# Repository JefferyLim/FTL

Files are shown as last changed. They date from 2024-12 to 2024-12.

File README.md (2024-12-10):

# Follow the Light

Follow the Light (FTL) is the final project for ENG EC545. The goal of this project was to explore the different course topics. Our team decided to explore the ideas of a IR-based communication project. Taking inspiration from TeraByte InfraRed Delivery ([TBIRD](https://www.ll.mit.edu/sites/default/files/other/doc/2023-02/TVO_Technology_Highlight_12_TBird.pdf)), we wanted to create a system that would transmit data to a receiver. The receiver, would utilize the sensor data to track and follow the transmitter.

We implemented many concepts that we learned from the course such as:
1. Finite State Machines
  - In order to build the message transmitter (preamble -> payload -> crc), reciever's motor control, receiver's scanning mode, and receiver's message parser
2. Modeling
  - To validate our designs to make sure our logic makes sense and works
3. Timing Analysis and WCET
  - Ensure that our design (and microcontroller) is capable of meeting the timing needs for the system. The ADC is critical for every subcomponent in the receiver, so it must always sample on time 
4. Datasheet and Specs
  - Because we worked with new hardware, we needed to understand the specs to would help us with our specifications

## Installation

Install the [Arduino IDE](https://support.arduino.cc/hc/en-us/articles/360019833020-Download-and-install-Arduino-IDE) and the [Teensyduino](https://www.pjrc.com/teensy/td_download.html) add-on.

FTL utilizes the following libraries. Utilize the `Import ZIP Library` feature on the Arduino IDE.

[RingBuffer Library](https://github.com/Locoduino/RingBuffer)

[ADC Library](https://github.com/pedvide/ADC)

[CRC](https://github.com/RobTillaart/CRC)

## Architecture

### Transmitter
transmitter_system drawio
The transmitter can be set in one of three modes:
1. LED Mode - A simple 50% duty cycle square wave used mostly for testing.
2. Message Mode - Takes a user's input, and transmit the message out.
3. Counter Mode - Increments a counter, and transmits the number. 

The transmitter works similarly to UART. It has a start bit, 8 bit preamble, 8 bit payload, and 8 bit CRC. The payload could be longer, but we chose to use 8 bits in order to debug it. 

### Receiver

reciever_system drawio

The receiver is comprised of three subsystems:
1. ADC Sampling - Samples the 3 photodiodes at 5x the transmit rate
2. Message Parsing - Parses 5 samples at a time to determine a `1` or a `0` bit
3. Motor Control - Moves the motor to maintain sight to the transmitter

We oversample the recieving signal in order to conduct a vote on the value of a bit. A specific part of the hardware is unable to meet high throughput, causing major skewing in the signal when the signal goes from 0 to 1. 

### Project Structure

```
.
├── ...
├── documentation           # Documentation
│   ├── drawio              # drawio diagrams
├── modeling                # modeling
├── software                # software
│   ├── adc_test            # initial testing for ADCs
│   ├── irled_tests         # initial testing for the IR LEDs
│   ├── receiver            # receiver code
│   └── transmitter         # transmitter code
└── README.md
```

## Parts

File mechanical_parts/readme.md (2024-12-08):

# Summary
Mechanical design, all parts were created using SolidWorks 2020.

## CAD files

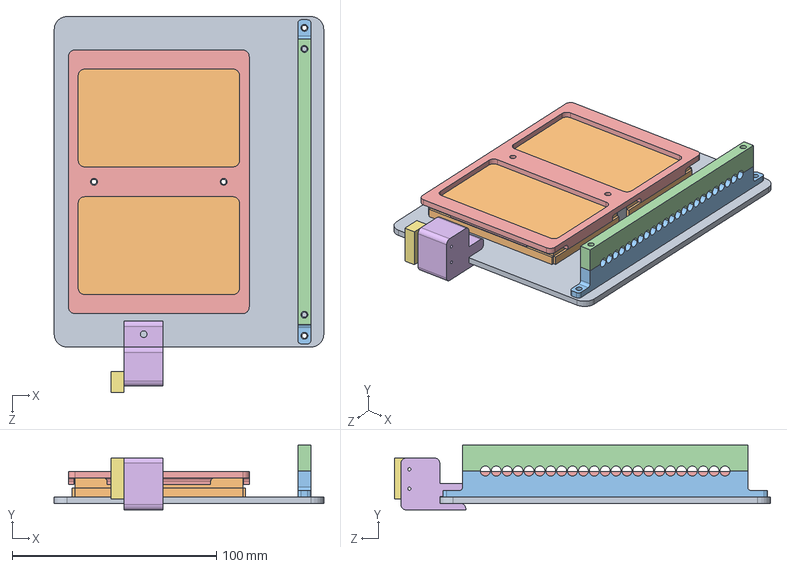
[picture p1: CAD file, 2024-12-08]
mechanical_parts/electronics assem.SLDASM
132.1 x 31.8 x 184.2 mm
electronics sled
small breadboard x 2
bottom_led_stockade
top_led_stockade
bb grabber
microswitch_holder
microswitch

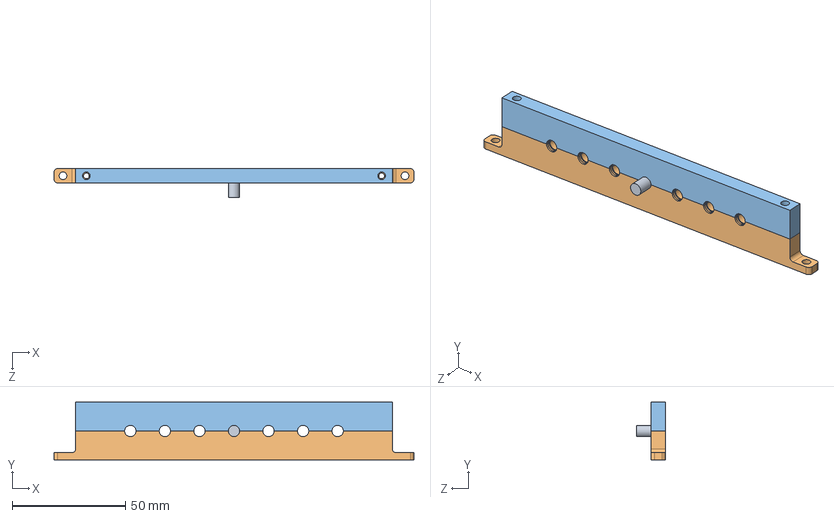
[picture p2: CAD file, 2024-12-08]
mechanical_parts/led_assem.SLDASM
158.8 x 25.4 x 12.7 mm
bottom_led_stockade v2
top_led_stockade v2

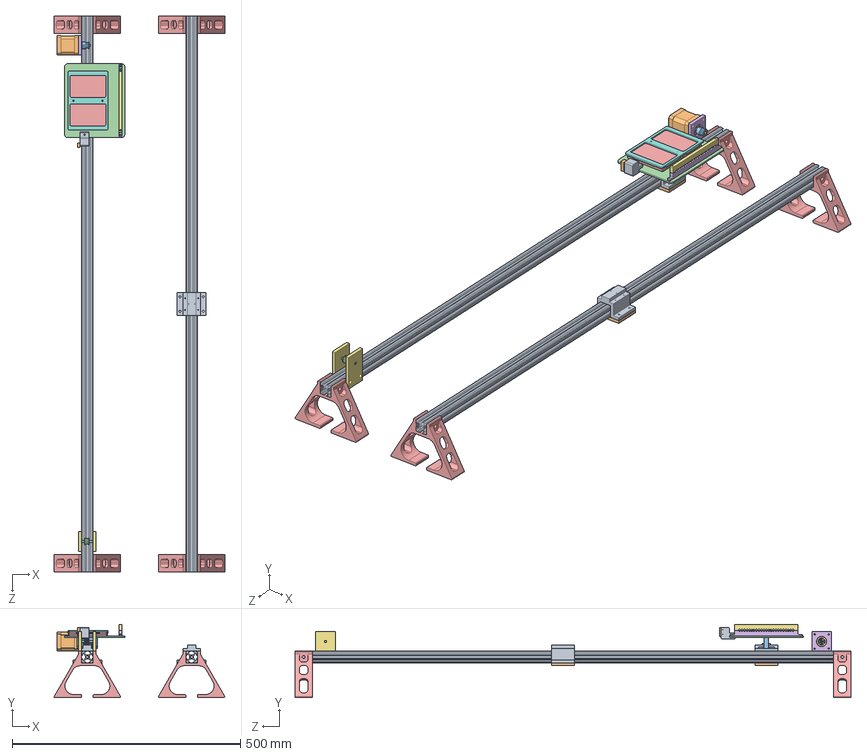
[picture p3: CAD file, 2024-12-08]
mechanical_parts/project_assem.SLDASM
374.6 x 160.1 x 1219.2 mm
47065T121_T-Slotted Framing x 2
nema_17_stepper
3684N12_Corrosion-Resistant HTD Timing Belt Pulley
3693N11_High-Strength HTD Timing Belt Idler Pulley
rail_support x 4
stepper plate
idler_plate x 2
idler_shaft
runner x 2
runner_bottom_plate x 2
runner_belt_grabber
electronics sled
small breadboard x 2
bottom_led_stockade
top_led_stockade
bb grabber
microswitch_holder
microswitch
attacher

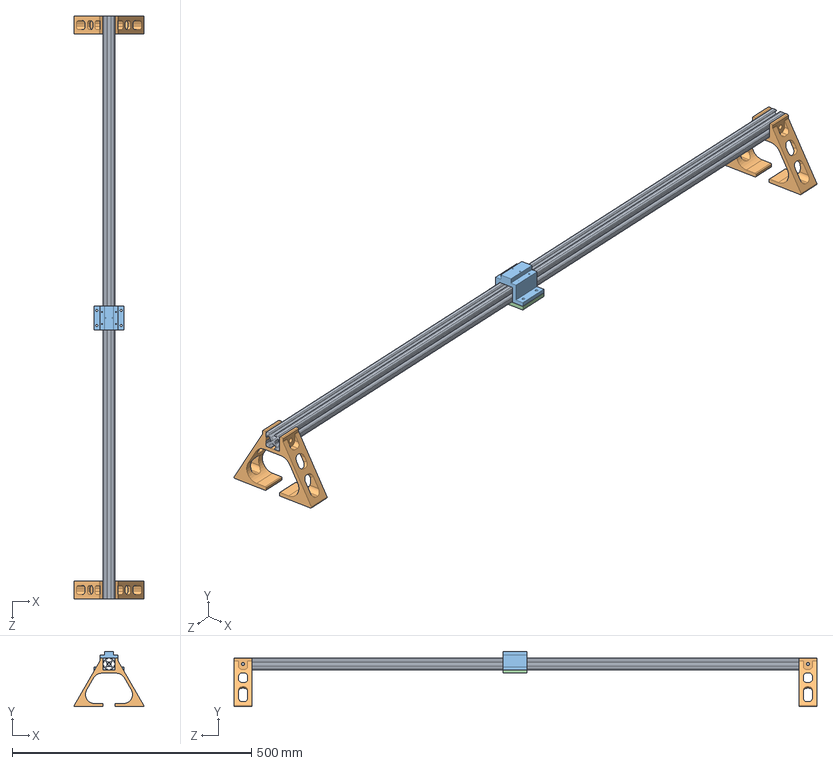
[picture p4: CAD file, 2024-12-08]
mechanical_parts/xmitter_assem.SLDASM
146.0 x 115.3 x 1219.2 mm
47065T121_T-Slotted Framing
rail_support x 2
runner
runner_bottom_plate

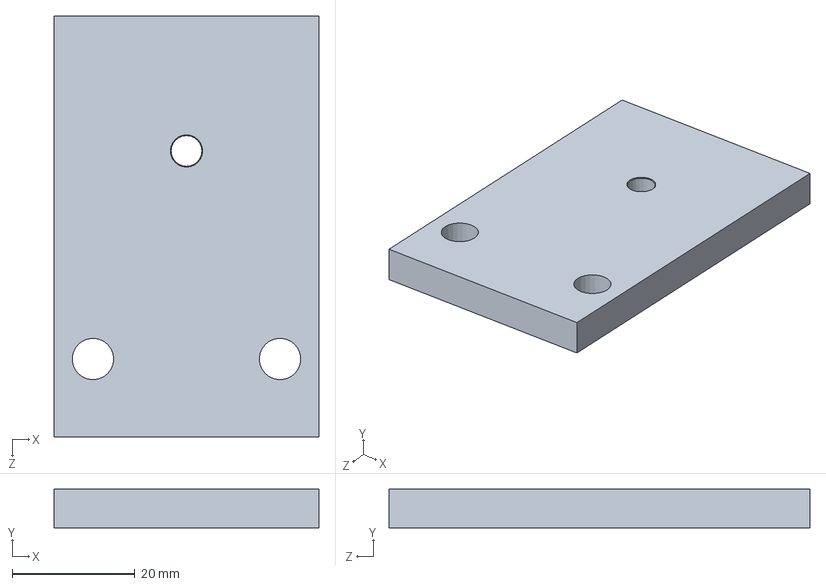
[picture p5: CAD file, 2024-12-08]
mechanical_parts/idler_plate.SLDPRT
43.2 x 6.35 x 68.6 mm

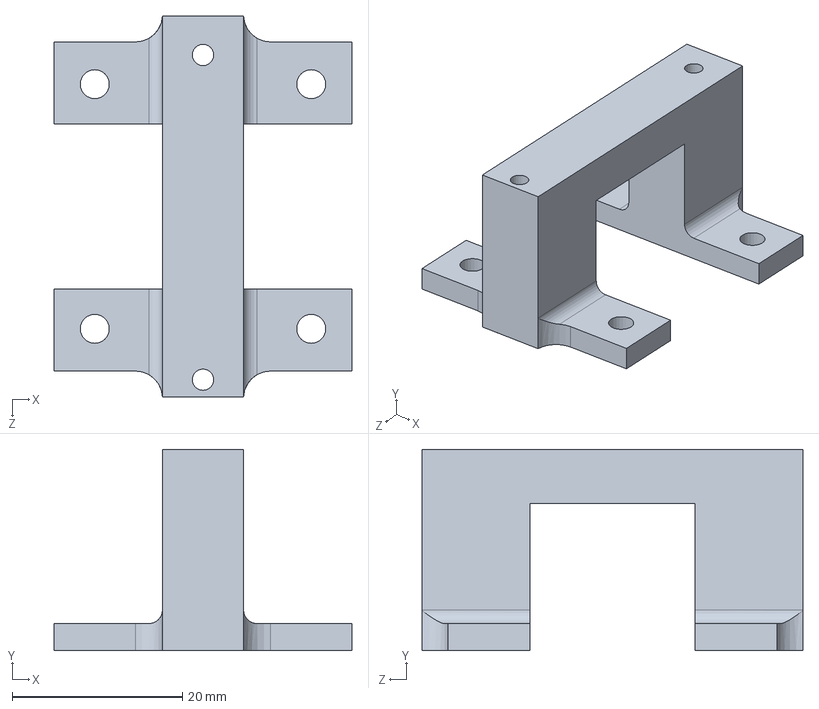
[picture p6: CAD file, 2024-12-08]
mechanical_parts/attacher.SLDPRT
34.9 x 23.6 x 44.7 mm

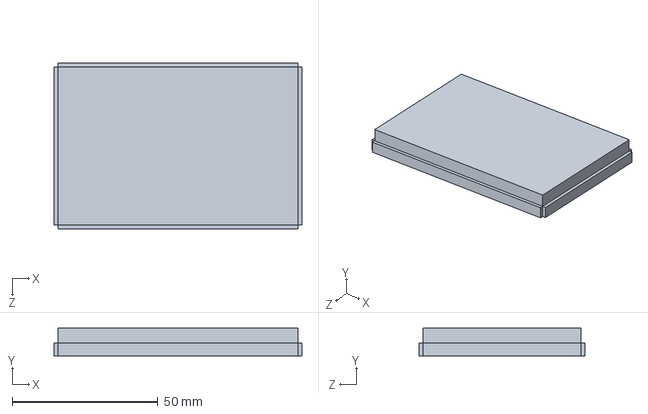
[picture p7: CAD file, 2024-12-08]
mechanical_parts/small breadboard.SLDPRT
84.9 x 9.53 x 57.0 mm

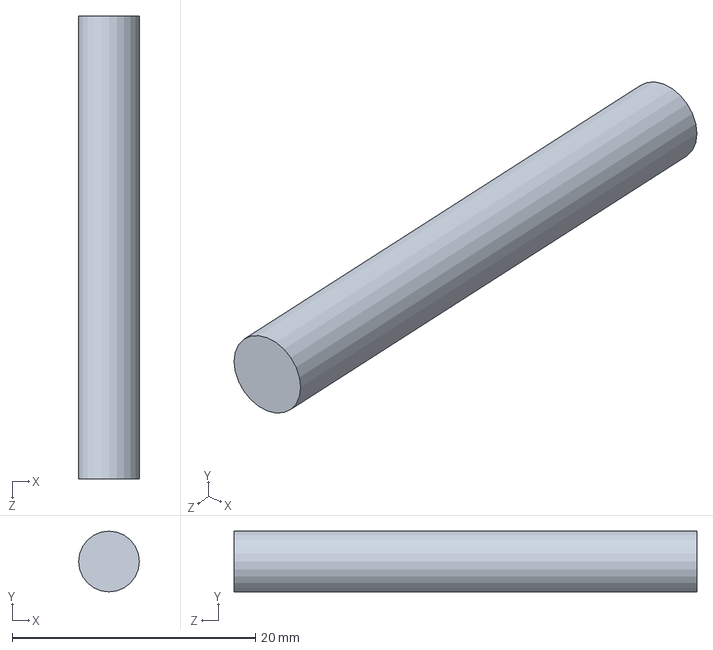
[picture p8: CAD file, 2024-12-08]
mechanical_parts/idler_shaft.SLDPRT
5.00 x 5.00 x 38.1 mm

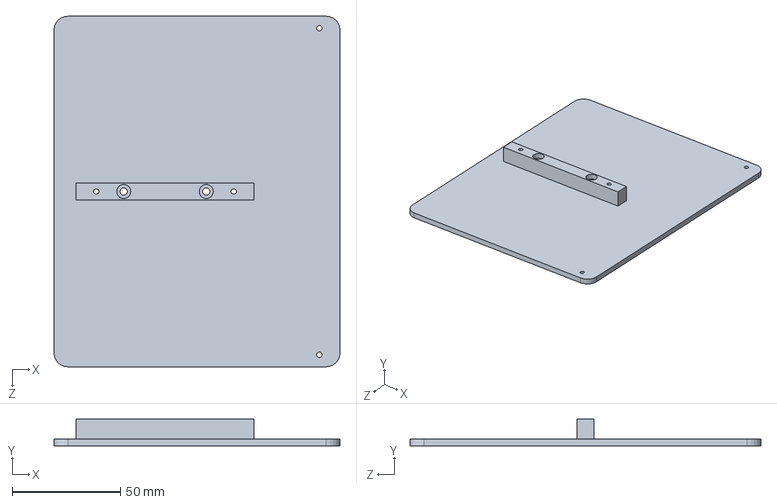
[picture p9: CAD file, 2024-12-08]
mechanical_parts/electronics sled.SLDPRT
132.1 x 12.4 x 161.9 mm

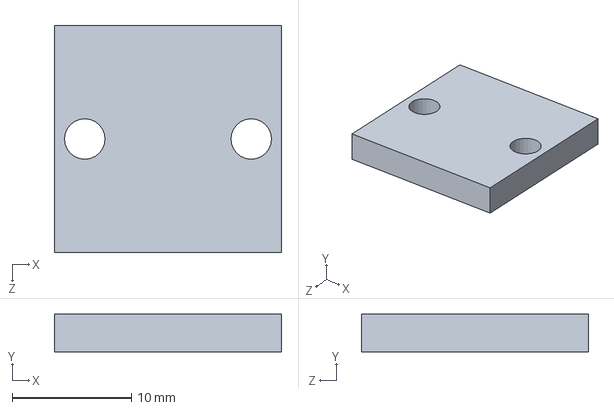
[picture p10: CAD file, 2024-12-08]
mechanical_parts/runner_belt_grabber.SLDPRT
19.1 x 3.17 x 19.1 mm

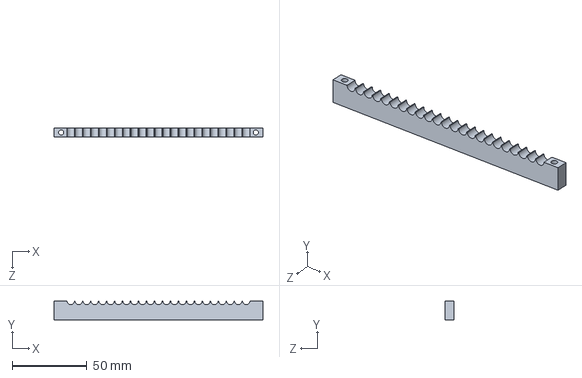
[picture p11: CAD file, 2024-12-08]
mechanical_parts/top_led_stockade.SLDPRT
139.7 x 12.7 x 6.35 mm

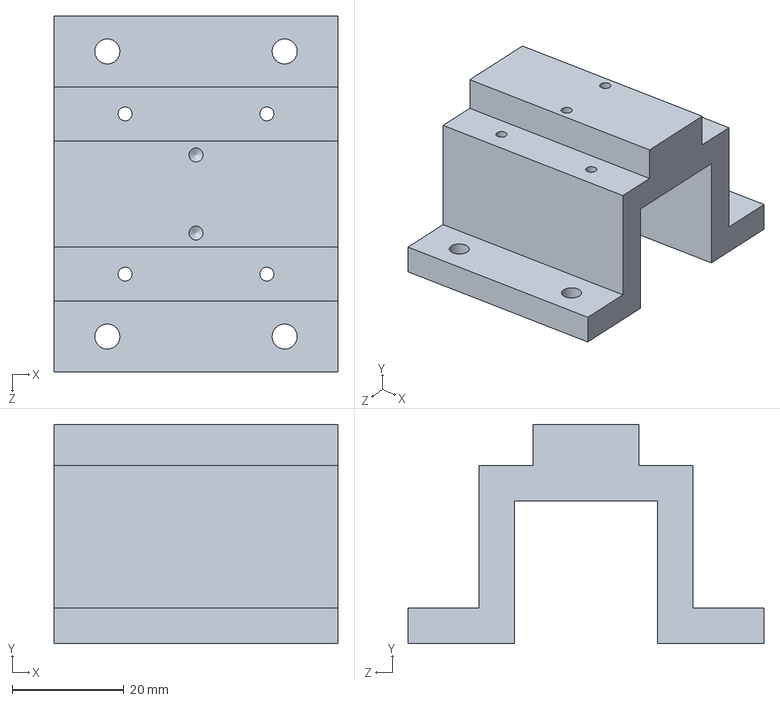
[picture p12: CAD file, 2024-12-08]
mechanical_parts/runner.SLDPRT
50.8 x 39.2 x 63.8 mm

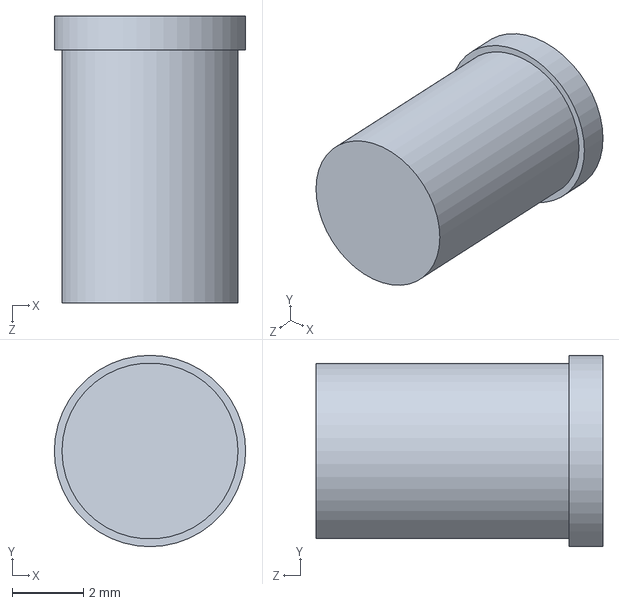
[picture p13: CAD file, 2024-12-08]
mechanical_parts/5mm_led_mock.SLDPRT
5.38 x 5.38 x 8.08 mm

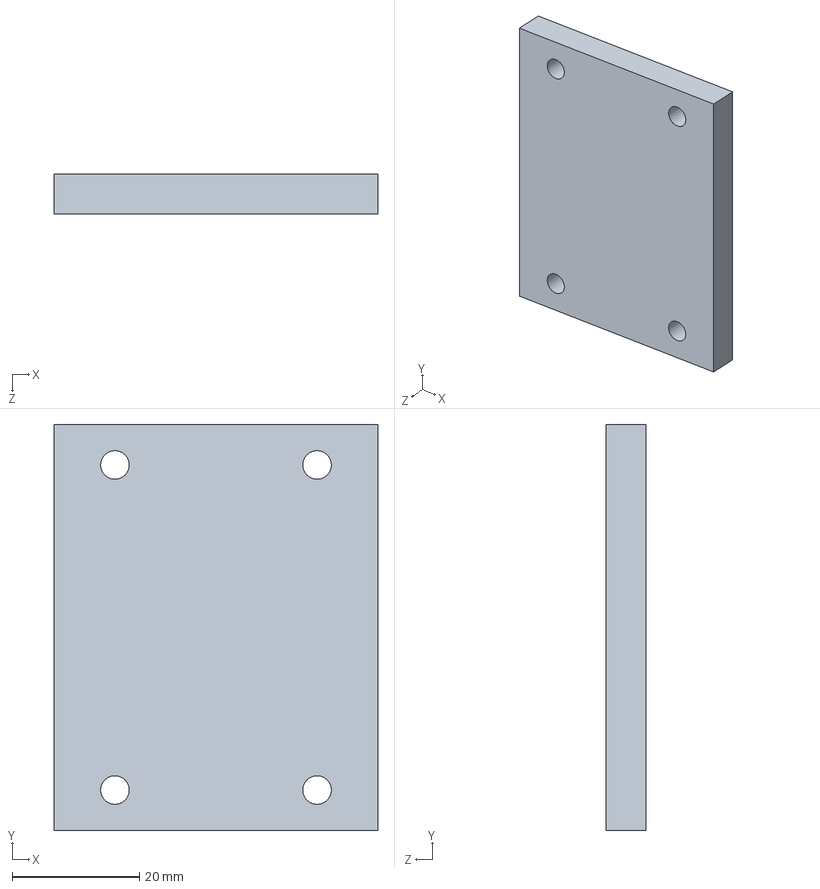
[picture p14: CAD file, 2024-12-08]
mechanical_parts/runner_bottom_plate.SLDPRT
50.8 x 63.8 x 6.35 mm

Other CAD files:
mechanical_parts/rail_support.SLDPRT
mechanical_parts/top_led_stockade v2.SLDPRT
mechanical_parts/microswitch_holder.SLDPRT
mechanical_parts/bottom_led_stockade.SLDPRT
mechanical_parts/3684N12_Corrosion-Resistant HTD Timing Belt Pulley.SLDPRT
mechanical_parts/3693N11_High-Strength HTD Timing Belt Idler Pulley.SLDPRT
mechanical_parts/47065T121_T-Slotted Framing.SLDPRT
mechanical_parts/6627T231_Stepper Motor.SLDPRT
mechanical_parts/bb grabber.SLDPRT
mechanical_parts/bottom_led_stockade v2.SLDPRT
mechanical_parts/microswitch.SLDPRT
mechanical_parts/nema_17_stepper.SLDPRT
mechanical_parts/stepper plate.SLDPRT

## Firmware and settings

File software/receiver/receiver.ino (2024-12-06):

#include "CRC8.h"

#define _PWM_LOGLEVEL_        0

#include <ADC.h>
#include <RingBuf.h>
#include <IntervalTimer.h>
#include <Teensy_PWM.h>

//Microswitch Pins
#define MOTOR_SIDE_SWITCH 22
#define OTHER_SIDE_SWITCH 21

#define USING_FLEX_TIMERS      true //Using flex timers for HW PWM

#define M2  9
#define M1  10
#define M0  11
#define STEP_PIN       7 //PWM Pins
#define DIR_PIN        6

//Threshold values
#define SENSOR_DIF_THRESH 200
#define SENSOR_SMALL_THRESH 50
#define SENSOR_BIG_THRESH 200

#define SENSOR_ON_THRESH 3600 // Sensor detecting for data
#define SENSOR_OFF_THRESH 3800 // Sensor not detecting for data

#define SENSOR_ABS_THRESH 3600 // Sensor not detecting for motor control

#define SAMPLING_FREQ 40000 // Hz
// Convert Sampling Frequency (Hz) to period (us)
double sampling_period = 1000000/SAMPLING_FREQ; // us

#define SAMPLING_RATIO 5 // SAMPLING_FREQ/
#define ON_THRESH 0 // SAMPLING_RATIO - ON_THRESH for 1's
#define OFF_THRESH 1  // OFF_THRESH for 0's

#define MOVEMENT_FREQ 500
 
//PRINT_SAMPLE, PRINT_RAW, PRINT_BIT, PRINT_CHAR, PRINT_SCAN, PRINT_NONE
#define PRINT_CHAR

//Timers (to emulate multithreading)
IntervalTimer sensor_readTimer;
IntervalTimer motor_controlTimer;

const int left_pin = A0;
const int mid_pin = A1;
const int right_pin = A2;

ADC *adc = new ADC(); 

//PWM Values:
float frequency;
float dutyCycle;

Teensy_PWM* stepper; //Stepper object


const int ledPin = LED_BUILTIN; // the pin with a LED

//States
enum tracking_state{
  SCANNING,
  LOCKED,
};

enum position_state{
  LEFT, MID_LEFT, MID, MID_RIGHT, RIGHT, UNKNOWN,
};

enum receiver_state{
  INIT,
  SYNCH,
  LOST,
};

enum message_state{
  START,
  MESSAGE,
  CRC,
  END,
};

//Sensor variables
//State variables
tracking_state track_state = SCANNING;
position_state pos_state;
message_state msg_state = START;
receiver_state rcv_state = INIT;

volatile char incoming_counter[10];
volatile int incoming_counter_counter = 0;
volatile int lost_counts = 0;
volatile int last_counter = -1;
volatile int current_counter = 0;

// Created photodiode array struct
struct photodiode_array{
  uint16_t left;
  uint16_t mid;
  uint16_t right;
  uint8_t bit : 1;
  uint8_t bit_confidence : 1;
  uint8_t : 3;
  uint8_t position : 3;
  
};

// RingBuffers
RingBuf<photodiode_array, 1024> adcBuffer; // for raw ADC outputs + other metrics
RingBuf<photodiode_array, 1024> bitBuffer; // extra buffer before message parsing
RingBuf<photodiode_array, 1024> motorBuffer; // extra buffer before motor control
RingBuf<int, 1024> messageBuffer; // buffer for collecting bits for message parsing

// Counters
int lostLockCount = 0;
int messageByteCount = 0;
int missingStartCounter = 0;

// Received Message
int receivedByte = 0;
int crcByte = 0;
CRC8 crc;
volatile int crc_index;
volatile int crccode;

// Flags
volatile bool bufferOverflow = 0;

// Performance Calcs
volatile int start = 0;
volatile int end = 0;

volatile unsigned long startMillis;
volatile unsigned long currentMillis;

// Position/Motor
int movement_counter = 0;
volatile position_state previous_position = MID;
volatile position_state last_known_state = MID;
int current_speed = 0;
bool hit_wall = false;
int button_debounce = 0;

void setup() {
  pinMode(left_pin, INPUT);
  pinMode(mid_pin, INPUT);
  pinMode(right_pin, INPUT);
  pinMode(ledPin, OUTPUT);
  Serial.begin(115200);

  ///// ADC0 ////
  adc->adc0->setAveraging(4); // set number of averages
  adc->adc0->setResolution(16); // set bits of resolution
  adc->adc0->setConversionSpeed(ADC_CONVERSION_SPEED::HIGH_SPEED); // change the conversion speed
  adc->adc0->setSamplingSpeed(ADC_SAMPLING_SPEED::HIGH_SPEED); // change the sampling speed

  ///// ADC1 ////
  adc->adc1->setAveraging(4); // set number of averages
  adc->adc1->setResolution(16); // set bits of resolution
  adc->adc1->setConversionSpeed(ADC_CONVERSION_SPEED::HIGH_SPEED); // change the conversion speed
  adc->adc1->setSamplingSpeed(ADC_SAMPLING_SPEED::HIGH_SPEED); // change the sampling speed

  sensor_readTimer.priority(0); //Set sensor priority higher
  motor_controlTimer.priority(1);
  
  sensor_readTimer.begin(read_sensors,(int)sampling_period); 
  motor_controlTimer.begin(pwm_control,(int)sampling_period*MOVEMENT_FREQ);

  //// PWM ////
  pinMode(DIR_PIN, OUTPUT);
  pinMode(M0, OUTPUT);
  pinMode(M1, OUTPUT);
  pinMode(M2, OUTPUT);
  stepper = new Teensy_PWM(STEP_PIN, 500, 0);
  /////

  //Microswitch pins
  pinMode(MOTOR_SIDE_SWITCH, INPUT_PULLUP);
  pinMode(OTHER_SIDE_SWITCH, INPUT_PULLUP);

}

void read_sensors() { //Read analog sensor input
  start = micros();
  struct photodiode_array dataset = {0}; 

  // difference variables
  // int edge_dif;
  // int left_mid_dif;
  // int mid_right_dif;

  dataset.left = adc->adc0->analogRead(left_pin);
  dataset.mid = adc->adc1->analogRead(mid_pin);
  dataset.right = adc->adc0->analogRead(right_pin);

  if(dataset.left <= SENSOR_ON_THRESH || dataset.right <= SENSOR_ON_THRESH \
   || dataset.mid <= SENSOR_ON_THRESH){
    dataset.bit = true;
    
    #ifdef PRINT_RAW
    Serial.print(1);
    #endif
    dataset.bit_confidence = true;
  }else if(dataset.left >= SENSOR_OFF_THRESH && dataset.right >= SENSOR_OFF_THRESH \
    && dataset.mid >= SENSOR_OFF_THRESH) {
    dataset.bit = false;
    dataset.bit_confidence = true;
    
    #ifdef PRINT_RAW
    Serial.print(0);
    #endif
  }else{
    
    #ifdef PRINT_RAW
    Serial.print(0);
    #endif
    dataset.bit = false;
    dataset.bit_confidence = false;
  }

  // edge_dif = dataset.left - dataset.right;
  // left_mid_dif = dataset.left - dataset.mid;
  // mid_right_dif = dataset.mid - dataset.right;

if(dataset.left > SENSOR_ABS_THRESH && dataset.mid > SENSOR_ABS_THRESH && dataset.right > SENSOR_OFF_THRESH){
    dataset.position = UNKNOWN;
  }else{

    if(dataset.mid < dataset.left && dataset.mid < dataset.right){
      dataset.position = MID; 
    }

    if(dataset.left < dataset.mid && dataset.left < dataset.right){
      dataset.position = LEFT; 
      if(abs(dataset.mid - dataset.left) < SENSOR_SMALL_THRESH){
        dataset.position = MID_LEFT;
      }
    }

    if(dataset.right < dataset.mid && dataset.right < dataset.left){
      dataset.position = RIGHT;
      if(abs(dataset.mid - dataset.right) < SENSOR_SMALL_THRESH){
        dataset.position = MID_RIGHT;
      }
    }
  }

  if(!adcBuffer.push(dataset)){
    Serial.println("ERROR: Can't push to buffer");
  }

  end = micros();
  // Serial.print("ADC: ");
  // Serial.println(end - start);
}

// Print function for printing the photodiode struct
void print_photodiode_struct(struct photodiode_array input){
  Serial.print(input.left);
  Serial.print(" | ");
  Serial.print(input.mid);
  Serial.print(" | ");
  Serial.print(input.right );
  Serial.print(" | ");
  Serial.print(input.bit );
  Serial.print(" | ");
  Serial.print(input.bit_confidence );
  Serial.print(" | ");
  printPosition(input.position);
  Serial.print(" | ");
  printPosition(last_known_state);
  Serial.println();
}

void printPosition(int input){
  switch (input) {
    case LEFT:
      Serial.print("LEFT");
      break;
    case MID_LEFT:
      Serial.print("MID_LEFT");
      break;
    case MID:
      Serial.print("MID");
      break;
    case MID_RIGHT:
      Serial.print("MID_RIGHT");
      break;
    case RIGHT:
      Serial.print("RIGHT");
      break;
    default:
      Serial.print("UNKNOWN");
      break;
  }
}

int bitShift = 0;
void messageParse(){
  struct photodiode_array adcValues;
  int bitCount = 0;
  int receivedBit = 0;

  // Double check that buffer is >5
  if(bitBuffer.size() < SAMPLING_RATIO){
    return;
  }

  // If we are in a "LOST" state... try and find presence of a signal...
  // A presence of a signal is 5 '1's or IR LED ON 
  if(rcv_state == LOST || rcv_state == INIT){
    
    digitalWriteFast(ledPin, 1);
    for(int i = 0; i < SAMPLING_RATIO; i++){
      // Look at the next 5 values
      bitBuffer.peek(adcValues, i);
      // Note, that if the bit confidence is high, then we can use the these samples
      // We only want to use 5 confident bits for now...
      if(adcValues.bit_confidence == 1){
        bitCount += adcValues.bit;
      }else{
        bitCount = 0;
        break;
      }
    }
  
    // If we find at least 4 '1' samples, lets start parsing
    // Move from LOST -> SYNCH
    if(bitCount >= (SAMPLING_RATIO - ON_THRESH)){
      #ifdef PRINT_CHAR
      Serial.println("Sync");
      #endif
      rcv_state = SYNCH;
      bitCount = 0;
      
      incoming_counter_counter = 0;
    }else{
      bitBuffer.pop(adcValues);
    }
  }else if(rcv_state == SYNCH){
    digitalWriteFast(ledPin, 0);
    // Begin counting bits
    for(int i = 0; i < SAMPLING_RATIO; i++){
      bitBuffer.pop(adcValues);
      bitCount += adcValues.bit;
    }

    // Do a majority vote
    // Anything inbetween is ambiguous, and we will exit SYNCH
    if(bitCount >= SAMPLING_RATIO - ON_THRESH){
      messageBuffer.push(1);
    }else if(bitCount <= OFF_THRESH){
      messageBuffer.push(0);
    }else{
      #ifdef PRINT_CHAR
      Serial.println();
      Serial.print("Ambiguous bits: ");
      Serial.print(bitCount);
      Serial.println("; returning to LOST...");
      #endif
      bitCount = 0;
      rcv_state = LOST;
      lostLockCount++;
      messageBuffer.clear();
      missingStartCounter = 0;
    }

    // Parse the bits for the message
    if (messageBuffer.size() > 6){
      if(msg_state == START) {
        missingStartCounter++;
        // If we dont' find the start within 1 second, then we exit SYNCH
        if(missingStartCounter > SAMPLING_FREQ/10){
          #ifdef PRINT_CHAR
          Serial.println("Can't find start bit...");
          Serial.println("Receiver can't find start bit; returning to LOST...");
          #endif
          messageBuffer.clear();
          missingStartCounter = 0;
          rcv_state = LOST;
        }else{
          bitCount = 0;
          // Look for a 111110
          for(int i = 0; i < 6; i++){
            messageBuffer.peek(receivedBit, i);
            if(i != 5 && receivedBit == 0){
              break;
            }
            if(i == 5 && receivedBit == 0){
              bitCount = 5;
            }
          }

          // 5 1's + 1 0's means we found the start bit
          if(bitCount == 5){
            msg_state = MESSAGE;
            for(bitCount = 5; bitCount >= 0; bitCount--){
              messageBuffer.pop(receivedBit);
              #ifdef PRINT_BIT
              Serial.print(receivedBit);
              #endif
            }
            bitCount = 0;
            bitShift = 0;
            receivedByte = 0;
            missingStartCounter = 0;
            #ifdef PRINT_BIT
              Serial.print("||");
            #endif
          }else{
            messageBuffer.pop(receivedBit);
            #ifdef PRINT_BIT
            Serial.print(receivedBit);
            #endif
          }
        }
      // found start
      }else if (msg_state == MESSAGE){
        // Pop 8 bits for the message
        messageBuffer.pop(receivedBit);
        #ifdef PRINT_BIT
        Serial.print(receivedBit);
        #endif
        receivedByte |= (receivedBit) << (bitShift);
        
        bitShift++;
        if(bitShift >= 8){
          msg_state = CRC;
          bitShift = 0;
          #ifdef PRINT_CHAR
          if(receivedByte == 4){

            incoming_counter[incoming_counter_counter] = '\0';
            incoming_counter_counter = 0;
            current_counter = atoi(incoming_counter);       // Convert to int using atoi

            // For the first count, just ignore this...
            if(last_counter == -1){
              last_counter = current_counter;
            }else if(last_counter+1 != current_counter){
              lost_counts += current_counter - last_counter;
            }

            last_counter = current_counter;

            Serial.print(", Lost counts: ");
            Serial.print(lost_counts);



            Serial.println();
            
          }else{
            Serial.print((char)receivedByte);
            incoming_counter[incoming_counter_counter] = (char)receivedByte;
            incoming_counter_counter++;
          }
          #endif
          
          #ifdef PRINT_BIT
            Serial.print("/");
          #endif
          crc.add((uint8_t)receivedByte);
          crccode = crc.calc();
        }
      }else if (msg_state == CRC){
        // Pop 8 bits for the message
        messageBuffer.pop(receivedBit);
        #ifdef PRINT_BIT
        Serial.print(receivedBit);
        #endif
        crcByte |= (receivedBit) << (bitShift);

        bitShift++;
        if(bitShift >= 8){
            
          #ifdef PRINT_BIT
            Serial.print("/");
          #endif
          if(crccode != crcByte){
            Serial.print(" (ERROR: CRC does not match: ");
            Serial.print(crcByte, HEX);
            Serial.print(", Expected: ");
            Serial.print(crccode, HEX);
            Serial.println(")");
          }

          
          crcByte = 0;
          crc.restart(); //remove all previous letters from the CRC calculation
          msg_state = END;
        }
        
      // grabbed message, just peek to make sure there isn't any more '0's after...
      }else if (msg_state == END){
        messageByteCount++;
        messageBuffer.peek(receivedBit, 0);
        if(receivedBit == 0){
          Serial.println("Found extra 0...");
        }
        msg_state = START;

      }
    }
  }
  //end = micros();
  //Serial.println(end - start);
}

void setSpeed(int speed)
{
  if (speed == 0)
  {
    // Use DC = 0 to stop stepper
    stepper->setPWM(STEP_PIN, abs(speed), 0);
  }
  else
  {
    //  Set the frequency of the PWM output and a duty cycle of 50%
    digitalWrite(DIR_PIN, (speed < 0));
    stepper->setPWM(STEP_PIN, abs(speed), 50);
  }
}



// 0 -> full step
// 1 -> 1/2 step
// 2 -> 1/4 step
//..
// 7 0 -> 1/256 step
void stepMode(int mode){
  digitalWrite(M0, bitRead(mode, 0));
  digitalWrite(M1, bitRead(mode, 1));
  digitalWrite(M2, bitRead(mode, 2));
}



elapsedMicros sincePrint;
int last_direction = 0;
#define SPEED 800
#define SPEED1 600
void pwm_control(){
  start = micros();
  struct photodiode_array input;
  motorBuffer.pop(input);

  stepMode(0);
  switch (input.position) {
    case LEFT:
      current_speed = -SPEED;
      last_direction = 0;
      break;
    case MID_LEFT:
      stepMode(0);
      last_direction = 0;
      current_speed = -SPEED;
      break;
    case MID:
      if(input.mid < input.left && input.mid < input.right){
        current_speed = 0;
      }
      last_direction = 0;
      break;
    case MID_RIGHT:
      last_direction = 0;
      stepMode(0);
      current_speed = SPEED;
      break;
    case RIGHT:
      last_direction = 0;
      current_speed = SPEED;
      break;
    case UNKNOWN:
      // If the receiver is lost, then we have lost the signal entirely
      if(rcv_state == LOST){
        
        // If we know what the last direction was, we should pick an initial direction
        // and go that way
        if(last_direction == 0){
          last_direction = 1;
          //printPosition(last_known_state);
          if(last_known_state == RIGHT || last_known_state == MID_RIGHT){
            current_speed = SPEED;
          }else if(last_known_state == LEFT || last_known_state == MID_LEFT){
            current_speed = -SPEED;
          }else if(last_known_state == MID){
            current_speed = -SPEED;
          }
        }
      
        // debounce the button for wall detection
        if(hit_wall == true){
          button_debounce++;
          if(button_debounce >= 40){
            button_debounce = 0;
            hit_wall = false;
          }
        }

        // If either wall has been hit, then we want to change our direction
        if(digitalRead(MOTOR_SIDE_SWITCH) == LOW && hit_wall == false){
            hit_wall = true;
            button_debounce = 0;
            current_speed = SPEED;
        }else if(digitalRead(OTHER_SIDE_SWITCH) == LOW && hit_wall == false) {
            hit_wall = true;
            button_debounce = 0;
            current_speed = -SPEED;
        }

      }
      break;
    default:
      break;
  }

  // If we hit the wall, then we want to stop moving
  if(last_direction == 0){
    if(digitalRead(MOTOR_SIDE_SWITCH) == LOW){
      current_speed = 0;
    }else if(digitalRead(OTHER_SIDE_SWITCH) == LOW) {
      current_speed = 0;
    }
  }

  // Store the previous known position
  if(previous_position != UNKNOWN){
    last_known_state = previous_position;
  }

  // Obtain the latest position
  previous_position = input.position;

  setSpeed(current_speed);
  // end = micros();
  // Serial.print("Motor: ");
  // Serial.println(end - start);
}


int abc = 0;

void loop() {
  struct photodiode_array adcValues;

  if(bufferOverflow){
    Serial.println("ERROR: RingBuffer Overflow");
  }
  // Attempt to pop ADC values
  if(adcBuffer.pop(adcValues)){
    movement_counter++;
    if(movement_counter == MOVEMENT_FREQ){
      motorBuffer.pushOverwrite(adcValues);
      movement_counter = 0;
    }

    // motorBuffer.pushOverwrite(adcValues);

    #ifdef PRINT_SAMPLE
      print_photodiode_struct(adcValues);
    #endif
    // Pushing ADC bits to a buffer for messages
    if(!bitBuffer.push(adcValues)){
      Serial.println("ERROR: Can't push to bitBuffer");
    }
    // Parse the bit for a message
    if(bitBuffer.size() > 5){
      messageParse();
    }
    
  }
  
}

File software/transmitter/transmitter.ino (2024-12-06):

#include "CRC8.h"

CRC8 crc;
// Create an IntervalTimer object
IntervalTimer txTimer;

const int ledPin = LED_BUILTIN; // the pin with a LED
const int irPin = 2;            // the pin with IR diode

// messages for transmission
char* message;
int messageLength = -1;
int counter = 0; //ascii character
char count_msg[20];

#define MAX_BYTE_LENGTH 500

// Controls
volatile int baud = 4000;
volatile bool halt = 1;

// Transmit variables
int ledState = LOW;
volatile int bitCount = 0;
volatile int messageCount = 0;
volatile int crc_index;
volatile int crccode;

// States for transmitter mode and state
enum transmitter_mode{
  BLINK, MESSAGE, COUNTER,
};

enum transmitter_state{
  START, DATA, CRC, END,
};

transmitter_mode tx_mode = BLINK;
transmitter_state tx_state = START;

// functions called by IntervalTimer should be short, run as quickly as
// possible, and should avoid calling other functions if possible.
void transmitter() {
  if (!halt) {
    // toggle mode: blink LED
    if (tx_mode == BLINK) {
      if (ledState == HIGH) {
        ledState = LOW;
      } else {
        ledState = HIGH;
      }
      digitalWriteFast(ledPin, ledState);
      digitalWriteFast(irPin, ledState);
      messageCount = 0;
      tx_state = START;
      bitCount = 0;
    } else if (tx_mode != BLINK) {
      // transmitter mode: transmit message
      if(tx_state == START){
        bitCount++;
        //Send the preamble
        if(bitCount == 8){
          tx_state = DATA;
          bitCount = 0;
          digitalWriteFast(ledPin, LOW);
          digitalWriteFast(irPin, LOW);
        //send the start bit
        }else{
          digitalWriteFast(ledPin, HIGH);
          digitalWriteFast(irPin, HIGH);
        }
      }else if(tx_state == DATA){
         char currentByte = 0;
         int currentBit = messageCount % 8;

        if(tx_mode == MESSAGE){  
          currentByte = message[int(floor(messageCount / 8))];
          currentBit = messageCount % 8;
        }else{ // tx_mode == COUNTER
          sprintf(count_msg, "%d%c", counter, 4);
          messageLength = strlen(count_msg); 
          currentByte = count_msg[int(floor(messageCount / 8))];
          currentBit = messageCount % 8;
        } 
        
        #ifdef DEBUG
        //prints the current byte in ASCII
        if (currentBit == 0) {
          Serial.println(message[int(floor(messageCount / 8))]);
        }
        //prints the current byte in binary
        Serial.print(bitRead(currentByte, currentBit));
        #endif

        digitalWriteFast(ledPin, bitRead(currentByte, currentBit));
        digitalWriteFast(irPin, bitRead(currentByte, currentBit));
        messageCount++;

      //at the end of each byte
      if(messageCount % 8 == 0){
          #ifdef DEBUG
          Serial.println();
          #endif
          //create crc
          crc.add(currentByte);
          crccode = crc.calc();
          tx_state = CRC;
          crc_index = 0;
        }
      //set LEDs high so resting state is on
      }else if (tx_state == CRC){
        if (crc_index > 7) {
          
          digitalWriteFast(ledPin, HIGH);
          digitalWriteFast(irPin, HIGH);
          tx_state = END;
          if (messageCount >= messageLength * 8) { //end of the message -- NOT BYTE
            messageCount = 0;
            counter++;
          }
          crc.restart(); //remove all previous letters from the CRC calculation
        }else{
          #ifdef DEBUG
          Serial.println(bitRead(crccode, crc_index)); //prints the current bit of CRC code
          #endif
          digitalWriteFast(ledPin, bitRead(crccode, crc_index));
          digitalWriteFast(irPin, bitRead(crccode, crc_index));
        }
        crc_index++;
        
      }else if(tx_state == END){
        bitCount++;
        if(bitCount == 8){
          tx_state = START;
          bitCount = 0;
        }
      //write the CRC code to the LEDs
      }
    }
  }else{
    digitalWriteFast(ledPin, HIGH);
    digitalWriteFast(irPin, HIGH);
  }
}

// Usage print helper function
void usage() {
  Serial.println();
  Serial.println("FTL Transmitter");
  Serial.println("h          - prints this message");
  Serial.println("s          - start/stop transmitter");
  Serial.println("b [number] - set baud rate ");
  Serial.println("m [string] - set transmit message ");
  Serial.println("t          - set toggle mode");
}


void setup() {
  pinMode(ledPin, OUTPUT);
  pinMode(irPin, OUTPUT);
  // Enables fastest possible mode on pins 
  // https://forum.pjrc.com/index.php?threads/high-speed-digital-i-o-in-teensy-4-1.75179/
  CORE_PIN13_PADCONFIG |= 0xF9;
  CORE_PIN19_PADCONFIG |= 0xF9;
  Serial.begin(1000000);
  txTimer.begin(transmitter, baud);  // transmitter to run every 1 seconds
  usage();
}

// Parse user input for baud (really any integer)
int parseInput() {
  int i = 0;
  char incomingByte;
  const byte numChars = 16; // arbitrary size...
  char receivedChars[numChars];

  while (Serial.available() != 0) {
    incomingByte = Serial.read();
    // ignore spaces...
    if (incomingByte != ' ') {
      receivedChars[i] = incomingByte;
      i++;
    }
  }
  receivedChars[i] = '\0'; // null terminate 
  return atoi(receivedChars); //return integer
}

// Parse a message for the transmitter
void parseMessage() {
  int i = 0;
  char incomingByte;
  char tempChars[MAX_BYTE_LENGTH]; // support up to 100 bytes (arbitrary)

  while (Serial.available() != 0 && i < MAX_BYTE_LENGTH) {
    delay(10);
    incomingByte = Serial.read();
    Serial.print(incomingByte);
    if (incomingByte == '\n') {
      tempChars[i] = 4;
      i++;
      break;
    }
    tempChars[i] = incomingByte;
    i++;
  }
  tempChars[i] = '\0';

  messageLength = i;
  // Free message before allocating
  free(message);
  message = (char*)malloc(sizeof(char) * (messageLength + 1));
  while (i >= 0) {
    message[i] = tempChars[i];
    i--;
  }
}

void flushInput() {
  while (Serial.available() > 0) Serial.read();
}
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

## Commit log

2024-11-06 Initial commit of teensy
2024-11-07 Adding case statements
2024-11-11 Further cleanup of messages and code
    - TODO: Fix input messages
    - TODO: set the proper timer for baud
    [transmitter.ino]
2024-11-11 Fixing baud calculator and toggling messages
    [transmitter.ino]
2024-11-20 Fixing the 1 and 0s of the transmission
    [transmitter.ino]
2024-11-20 Reverted '1' to being LED on
    - Need LED on to signify when we're in the presence of transmitter
    - Otherwise, we would lose the signal
    [transmitter.ino]
2024-11-23 Fixing off by 1 bug in crc
    [transmitter.ino]
2024-11-23 Fixing bug with crc
    - Tasha was right, Jeff is dumb
    - Extra bit Jeff found was in another state
    [transmitter.ino]
2024-11-23 Receiver (#3)
    * Direction state machine
    Attempt at using timers to emulate multithreading (Arduino does not have true threads), still needs work and commenting
    * Direction code update
    Detects position of TX or lack of signal
    * Work in progress
    * Update direction_test.ino
    * Moving directories
    * Adding RingBuffer and correct analogRead
    * Adding required libraries in README
    * Cleanup
    - Removed unnecessary flags
    - Changed definitions to all caps
    - Renamed variables to make more sense
    * Moving position and bit eval into interrupt
    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
    [adc_test.ino]
2024-12-05 Receiver (#4)
    * Adding isr direction
    * Added bit parsing at a 5:1 ratio
    * Adding message parsing
    - Assumes 1 to 10 clock ratio
    * Reve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
2024-12-08 Mechanical parts (#6)
    * Create readme.md
    * added mechanical parts
    * Update readme.md
    ---------
    [3684N12_Corrosion-Resistant HTD Timing Belt Pulley.SLDPRT, 3693N11_High-Strength HTD Timing Belt Idler Pulley.SLDPRT, 47065T121_T-Slotted Framing.SLDPRT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]
2024-12-11 Create flowgraph folder
